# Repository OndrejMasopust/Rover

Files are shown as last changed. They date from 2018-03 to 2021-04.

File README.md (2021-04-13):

# Rover
This repository contains my school project. It is a remote control car with rotating lidar. The car is controled from a custom Java app.   
If you want the documentation to be translated into English, raise an issue and I will try to translate it as soon as possible. ;-)

[Link](https://ondrejmasopust.github.io/Rover/) to the official website with a documentation.

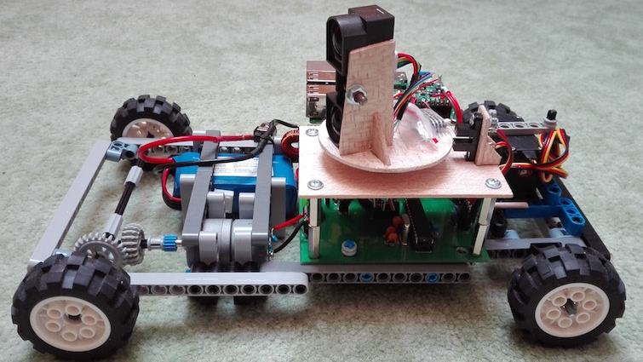
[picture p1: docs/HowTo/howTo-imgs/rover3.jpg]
Rover
   
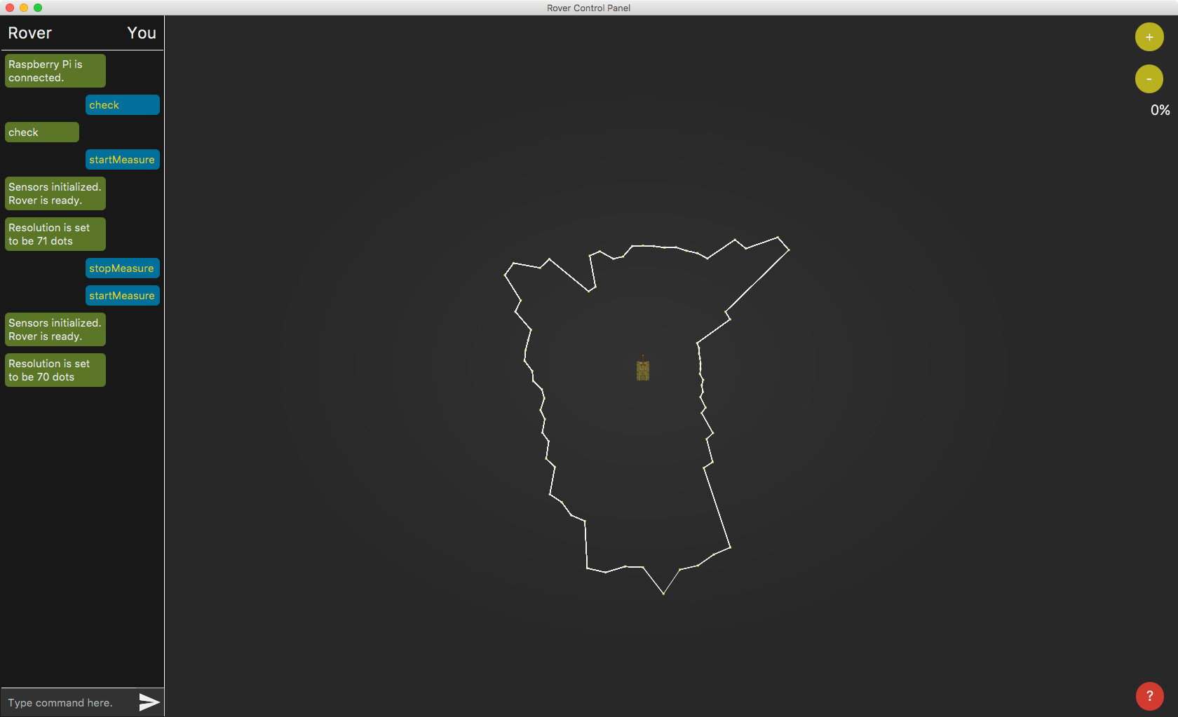
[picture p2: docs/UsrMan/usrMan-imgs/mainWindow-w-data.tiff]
main-Screen-w-data


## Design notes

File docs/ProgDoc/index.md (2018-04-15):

# Programátorská dokumentace
[Java dokumentace](JavaDoc/index.html)   
[Python dokumentace](PythonDoc/index.html)   
[C dokumentace](CDoc/index.html)

`Jar` soubor s řídící aplikací je možné najít na [tomto odkazu](https://github.com/OndrejMasopust/Rover/blob/master/Java/build/dist/RoverControlPanel.jar).   
Program pro Raspberry Pi lze nají v [této složce](https://github.com/OndrejMasopust/Rover/tree/master/Python/src) (složky s názvem `test` nejsou pro běh programu nutné).   
Firmware pro ATMega 168 je na [tomto odkazu](https://github.com/OndrejMasopust/Rover/tree/master/AVR/firmware).

# Popis fungování

## Autíčko
### Úvod
Autíčko je postavené nad platformou Raspberry Pi, která obstarává většinu operací. Jako programovací jazyk pro Raspberry jsem si zvolil Python, jelikož je pro tuto platformu nejvíce podporován.
Pro konverzi analogových dat ze senzoru do digitální podoby je použit mikrokontrolér ATMega 168 od firmy MicroChip.
Obousměrný provoz motorů obstarává integrovaný obvod L293D od firmy Texas Instruments.

### Napájení
Celé autíčko je napájeno baterií typu Li-pol se 3
články a kapacitou 1300mAh. Provozní doba autíčka na jedno nabití by teoreticky mohla být klidně přes 2 hodiny (průměrná spotřeba byla naměřena okolo 500mAh). Konverzi napětí z úrovně baterky na
úroveň "příjemnou" obvodům a motorům obstarávají integrované obvody LM2576 též od firmy Texas Instruments. Jsou použity dvě verze tohoto obvodu. První verze je pro konverzi napěťové úrovně na
fixní napětí 5V pro napájení "logiky". Druhá verze s nastavitelným výstupním napětím dodává 6V pro napájení motorů. Tyto obvody vyžadují několik dalších pasivních součástek pro správné fungování.
Ty jsou na plošném spoji v blízkosti samotných LM2576 (oblasti okolo cívek).

Obvody LM2576 jsou tzv. spínané zdroje napětí. To znamená že výstupní napětí je upravováno pomocí PWM (pulse width modulation). To má za důsledek efektivní konverzi napětí (dokumentace uvádí
účinnost až 77%). Dalším druhem napěťových regulátorů jsou tzv. lineární regulátory, které ovšem fungují v podstatě jako proměnné rezistory a nejsou tudíž moc efektivní. Přebytečnou elektrickou
práci vyzáří ve formě tepla. Proto jsem se rozhodl pro spínaný zdroj oproti lineárnímu regulátoru.

### Zatáčení
Zatáčecí mechanismus je řešen servem od firmy Hitec. Mechanismus zatáčení jsem okopíroval z Lego stavebnice
["Dump Truck"](https://www.lego.com/en-us/service/buildinginstructions/search?initialsearch=8415#?text=8415). Servo je ovládáno z Raspberry Pi pomocí tzv. PWM (pulse width modulation). Jelikož je
pro ovládání serva potřeba velké preciznosti signálu, zvolil jsem pro tento účel knihovnu [pigpio](http://abyz.me.uk/rpi/pigpio/). Tato knihovna poskytuje API, které umožňuje
snadné ovládání serva zadáním délky služebního cyklu (duty cycle). Pro hodnotu `1500` se ručička serva nastaví do střední polohy. Bezpečné meze otáčení z hlediska serva je interval <1000; 2000>.
Ovšem pro konkrétní potřeby Roveru je tento interval omezen.

### Pohyb
Pohyb autíčka obstarává stejnosměrný motor uložený vedle baterie. K jeho ovládání je použit již zmíněny obvod L293D. Ten přijímá signál PWM (pulse width modulation) od Raspberry a podle toho je
schopen upravit napětí proudící do motoru. Možnosti měnit napětí jdoucí do motoru není ovšem využito. Do motoru tedy jde buď 6V, nebo 0V.

L293D ovšem obstarává ještě jednu důležitou funkci a tou je možnost změny polarity výstupu k motoru a tudíž změna směru otáčení motoru. Toho je docíleno pomocí tzv. "H můstku" (H-bridge)
uvnitř L293D. Pro jistotu je k němu připojen pasivní kovový chladič jako prevence přehřátí.

### Senzor
Jako senzor vzdálenosti jsem použil výrobek firmy Sharp. Konkrétně ten s označením `GP2Y0A710K0F`. Měří vzdálenost pomocí paprsku světla. Jeho nevýhodou ovšem je, že má rozsah jen 100cm až 500cm.
Vzdálenosti menší než 100cm se budou na výstupu jevit jako vyšší a nelze je odlišit. Pro měření vzdáleností kratších než 100cm by bylo potřeba využít jiného senzoru.

Rotace senzoru je řešena pomocí stejnosměrného motoru. Přenos dat z rotujícího senzoru je řešen pomocí tzv. "slip ring". Ten umožňuje elektrický kontakt mezi dvěma navzájem rotujícími objekty.
Jelikož je motor stejnosměrný a není tedy žádná zpětná vazba ohledně jeho aktuální polohy, obsahuje držák senzoru i optozávoru. Ta se stará o informování Raspberry o tom, že senzor vykonal jednu
otáčku. Optozávora se skládá z LED diody a fototranzistoru. Když je paprsek světla z diody do tranzistoru přerušen výstupkem na senzorovém kotouči, tranzistor se uzavře a tím vyšle signál do
Raspberry. To je uvnitř nastaveno tak, aby tyto signály zpracovalo náležitým způsobem.

Aby mohla řídící aplikace správně vizualizovat data, je nutné na začátku měření provést několik "volných otáček", kdy nejsou data ze senzoru vyžadována. Během těchto rotací se motor dostane na
konstantní rychlost otáčení a v Raspberry Pi je změřena doba jedné otáčky na základě prodlevy signálů z optozávory. Ta je poté vydělena dobou jednoho měření senzoru a výsledkem je počet měření
během jedné otáčky. Jedno měření trvá dle dokumentace přibližně 20ms a s touto hodnotou se také pracuje v programu. Jiná možnost, jak být od senzoru upozorněn na novou naměřenou hodnotu není.

Vypočítané rozlišení se poté
pošle řídící aplikaci a slouží ke správnému umístění později přijatých dat na obrazovku. Raspberry také po každém vykonání otáčky senzoru pošle do řídící aplikace příkaz k resetování indexu měření,
aby aplikace znovu začala umisťovat naměřená data od počátečního pozice a nedošlo k pootočení obrazu vykreslovaném v aplikaci (více o tom později).

Výstup
senzoru je řešen analogově. Podle naměřené vzdálenosti se mění úroveň napětí na výstupu. O konverzi toho analogového výstupu do digitální podoby se, jak už jsem zmínil, stará mikrokontrolér ATMega
168.

### ATMega 168
Mikrokontrolér ATMega 168 je naprogramován v jazyce C a k jeho časování je použit krystal o frekvenci 16MHz. Komunikace s Raspberry Pi je řešena pomocí protokolu I<sup>2</sup>C. Raspberry Pi je
v této komunikace v roli tzv. "master" a ATMega jako tzv. "slave". Jelikož ATMega není schopno
vykonávat více procesů najednou, je jeho program řešen pomocí tzv. přerušení (interrupts). Na samotném začátku programu je provedena jedna konverze, která se uloží a ATMega čeká na pokyn od Raspberry. Když
si Raspberry vyžádá data, ATMega mu pošle data z poslední konverze a provede konverzi novou. Poté znovu čeká na vyžádání dat přes I<sup>2</sup>C. Komunikaci přes I<sup>2</sup>C je na straně
Raspberry Pi řešena pomocí knihovny [smbus2](https://pypi.python.org/pypi/smbus2/0.2.0).

Zpracování dat v Raspberry Pi spočívá v přepočtení přijaté relativní hodnoty na volty a poté pomocí dané funkce přepočtení voltů na centimetry. Funkce byla stanovena pomocí
zpracování pokusných naměřených hodnot v programu Microsoft Office Excel. Přepočtená data se posílají přes TCP protokol do řídící aplikace na operátorově počítači, kde se vizualizují.

### Příkazy
Příkazy, které může Rover řídící aplikaci posílat jsou následující:

#### rd
Tento příkaz slouží k informování operátora o tom, že již byly provedeny "volné otáčky". Jde o zkratku slova "ready".

#### ro
Příkaz `ro` je vždy následován celou číslovkou, která označuje počet měření během jedné otáčky. Tento příkaz je spolu s příkazem `rd` posílán vždy po dokončení "volných otáček". Příkaz zvolen
jako zkratka slova "resolution".

#### dt
Příkaz `dt` slouží k přenosu naměřených hodnot. Je následován celou číslovkou označující vzdálenost v centimetrech. `dt` je zkratka slova data.

#### rc
Tento příkaz je poslán Roverem vždy po dokončení jedné otáčky a instruuje řídící apliakci, že následující data má zobrazovat od počátečního bodu s indexem 0. Jde o synchronizaci, aby nedošlo k
pootočení vizualizovaného obrázku (více o tom později). Jde o zkratku slovního spojení "reset dot counter".

#### er
Příkaz `er` je vždy následován chybovou hláškou, která se má zobrazit v konzoli řídící aplikace. Tato zpráva bude v červené bublině, aby se odlišilo, že jde o chybu. `er` je zkratka pro "error".

#### bt
Tento příkaz zatím Rover neposílá, ale řídící aplikace ho umí zpracovat. Jde o změnu ukazatele stavu baterie v řídící aplikaci. Zpětná vazba o stavu baterie není v zadání práce a není zatím funkční.
Příkaz by měl být vždy následován číslem, které se má v ukazateli zobrazit a byl zvolen jako zkratka slova "battery".

## Řídící aplikace
Řídící aplikace je naprogramována v jazyce Java. Grafické rozhraní je vytvořeno pomocí API JavaFx. Neúspěšný pokus o navázání komunikace s Roverem je na začátku běhu programu řešen nekonečnou
smyčkou, kdy se program stále snaží komunikaci navázat. Pokud chce uživatel zastavit pokusy o navázání komunikace, musí sám aplikaci ukončit. Jak již bylo zmíněno v uživatelské dokumentaci,
ovládací aplikace obstarává vizualizaci dat ze senzoru a bezdrátové ovládání pohybu autíčka.

Po připojení k Roveru běží aplikace na 2 vláknech. První se stará o grafické rozhraní a to druhé o přijímání zpráv od Roveru. Pokud přijde zpráva od Roveru, komunikační vlákno ji předá grafickému
vláknu, které poté zprávu buď zobrazí v konzoli na levé straně obrazovky, nebo vykoná daný příkaz. Některé příkazy od Roveru se v konzoli nezobrazují z úsporných důvodů.

### Systém vizualizace dat
Data z měření jsou z Roveru posílána bez informace o jejich úhlové poloze. Jedinou synchronizaci poskytuje příkaz `rc`. Z tohoto důvodu si řídící aplikace spočítá úhel mezi jednotlivými měřeními na
základě přijatého rozlišení (příkaz `ro`) poté, co Rover dokončí "volné otáčky". Tento úhel se nadále používá pro všechna přijatá měření. Řídící aplikace si ukládá vlastní čítač dat, který se
vždy zvýší o jedno s každou přijatou hodnotou.
Na základě tohoto čítače je nastaven úhel zobrazených dat. Čítač je resetován po přijetí příkazu `rc` a následující přijaté měření je zobrazeno pod úhlem 0° (pozice za Roverem).

Pokud je předchozí měření viditelné, je spojeno s aktuálním měřením pomocí úsečky. To pomáhá představě o půdorysu okolí Roveru.

Vizualizovaná data je možné si přiblížit a oddálit pomocí tlačítek "+" a "-" v pravém horním rohu aplikace.

### Ovládání pohybu Roveru
Ovládat pohyb Roveru je možné z řídící aplikace pomocí mačkání šipek na klávesnici. Pokud je ovšem zrovna prováděna akce zápisu do textového pole pro zadávání příkazů, mačkání šipek nebude mít efekt
ovládání pohybu Roveru. Proto je vždy po odeslání příkazu z textového pole zaměření z toho textového pole odňata, aby bylo možné šipkami pohyb Roveru ovládat.

### Příkazy
Příkazy, které budou mít nějaký efekt po jejich zadání v řídící aplikaci jsou zobrazeny v konzoli žlutým fontem a jsou následující:

#### startMeasure
Tento příkaz instruuje Rover o tom, že má inicializovat senzorový motor a začít posílat data z měření.

#### stopMeasure
Příkaz `stopMeasure` naopak měření zastaví.

#### check
Teto příkaz slouží k ověření komunikace mezi Roverem a řídící aplikací. Pokud Rover ihned odpoví zprávou `check`, je spojení v pořádku. Pokud ne, nastala někde chyba.

#### $resPer
Příkaz `$resPer` slouží k resetování stavu baterie na 100%. Dolar na začátku značí, že jde pouze o interní příkaz. Tento příkaz není odesílán autíčku.

### Informační stránka
V aplikaci je v pravém dolním rohu tlačítko s otazníkem. To slouží ke zobrazení stručné informace ohledně příkazů popsaných výše.

# Zdroje

### Knihovny nestandardní pro použité programovací jazyky
- [Pigpio](http://abyz.me.uk/rpi/pigpio/)
- [smbus2](https://pypi.python.org/pypi/smbus2/0.2.0)
- [RPi.GPIO](https://pypi.python.org/pypi/RPi.GPIO)

### Programy
- [Eclipse IDE](https://www.eclipse.org)
- [Scene Builder](http://gluonhq.com/products/scene-builder/)
- [TextWrangler](https://www.barebones.com/products/textwrangler/)
- [Pandoc](https://pandoc.org)
- [Overleaf](https://www.overleaf.com)
- [ShareLaTex](https://cs.sharelatex.com)
- [Doxygen](http://www.stack.nl/~dimitri/doxygen/)
- [Apache Ant](https://ant.apache.org)
- [Lego Digital Designer](https://www.lego.com/en-us/ldd)

### Tutoriály
Uvedeny pouze ty "nejvíce klíčové" pro můj projekt.
- [JavaFx GUI](https://www.youtube.com/watch?v=FLkOX4Eez6o&list=PL6gx4Cwl9DGBzfXLWLSYVy8EbTdpGbUIG)
- [Java multithreading](https://www.itnetwork.cz/java/vlakna)
- [Python networking](https://www.youtube.com/watch?v=XiVVYfgDolU)
- [Python multithreading](https://www.tutorialspoint.com/python/python_multithreading.htm)
- [Python Event()](https://stackoverflow.com/questions/31247820/how-to-use-event-objects-in-python-with-a-thread)

### Barvy grafického rozhraní
- [Blackberry pallete](https://developer.blackberry.com/design/bb10/color.html)

### Webová stránka
Použito služby [GitHub Pages](https://pages.github.com)

### Obrázky
#### Odesílací šipka v hlavním okně řídící aplikace
<div>Icons made by <a href="https://www.flaticon.com/authors/google" title="Google">Google</a> from <a href="https://www.flaticon.com/" title="Flaticon">www.flaticon.com</a> is licensed by
<a href="http://creativecommons.org/licenses/by/3.0/" title="Creative Commons BY 3.0" target="_blank">CC 3.0 BY</a></div>
#### Obrázek tanku v hlavní okně řídící aplikace
Autor nevyžaduje být uveden. Uvedu tedy alespoň [odkaz na webovou stránku](http://2dgameartforfree.blogspot.cz/2014/09/top-down-extras-2-tank.html), kde lze obrázek stáhnout.

### Ostatní zdroje
Se schématem plošného spoje mi pomohl Ondřej Dvorský.   
S vyladěním programu pro Raspberry Pi mi pomohl vedoucí práce Vojtěch Horký.   
Oběma patří velké poděkování.

Výrobu plošného spoje obstarala firma [JLCPCB](https://jlcpcb.com).

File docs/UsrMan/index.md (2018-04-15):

# Rover
Rover je dálkově řízené autíčko s otočným lidarem. Ovládací aplikace umožňuje vizualizaci dat ze senzoru a ovládání autíčka.

## Autíčko
Hlavní konstrukce autíčka je sestavená z lego kostiček. Návod na sestavení můžete najít [zde](https://ondrejmasopust.github.io/Rover/HowTo/index.html). K sestavení je nutná znalost pájení.

Autíčko se zapne přepnutím přepínače vedle baterie. V tu chvíli by měly indikační LED diody na Raspberry Pi začít blikat. Je nutné chvíli počkat, než se Raspberry Pi načte a poté je možné
se k autíčku připojit přes Wi-Fi (stejně, jako byste se připojovali k běžné Wi-Fi např. u vás doma). V tuto chvíli ovšem není ještě možné autíčko ovládat. Je nutné spustit danou aplikaci, která
má běžet na Raspberry Pi. Toho se docílí tak, že se připojíte k Raspberry Pi přes `ssh` pomocí příkazové řádky:
```
ssh pi@raspberrypi.local
```
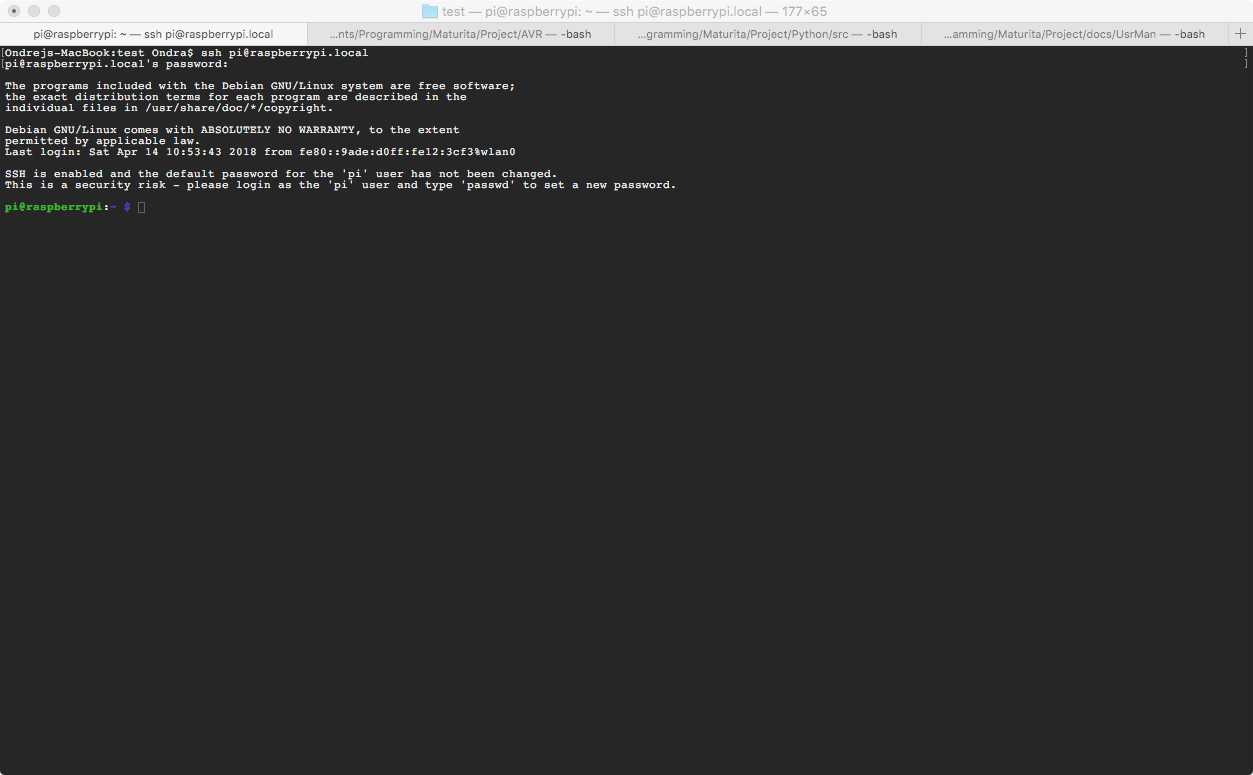
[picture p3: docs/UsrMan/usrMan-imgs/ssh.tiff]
ssh
   
Budete vyzváni k zadání hesla. Znaky se nebudou zobrazovat na obrazovce během toho, jak je budete zadávat. To je běžné chování a je to tak z bezpečnostních důvodů.

Až se přihlásíte do terminálu Raspberry Pi, přejděte pomocí příkazu `cd` do složky se souborem `Main.py`. V mém případě to znamená:
```
cd Documents/Ondra/Rover/src/com/masopust/ondra/python/main/
```
Nyní můžete spustit program pomocí příkazu:
```
python3 Main.py
```
V tuto chvíli program čeká, až se někdo pokusí s ním navázat komunikaci. Toho se docílí v počítačové aplikaci, která je součástí projektu. Pokud se připojení podaří, v terminálu se ukáže
(IP adresa a číslo portu se mohou lišit):
```
Connection from ('192.168.0.6', 54710) was successful
```

## Aplikace
Ovládací aplikace obstarává vizualizaci dat ze senzoru a bezdrátové ovládání pohybu autíčka. Aplikaci
lze spustit dojklikem na soubor `RoverControlPanel.jar`, který lze stáhnout [zde](https://github.com/OndrejMasopust/Rover/blob/master/Java/build/dist/RoverControlPanel.jar). Po spuštění aplikace budete vyzvání k zadání IP adresy autíčka a portu, přes který se chcete zkusit
k Raspberry Pi připojit. Pokud neznáte IP adresu autíčka, lze zadat `raspberrypi.local`. To by mělo též fungovat. Jako port uveďte číslo `5321`, pokud jste toto číslo nezměnili v programu, který
běží na Raspberry Pi. Po zadání hodnot stiskněte tlačítko `Connect`, nebo stiskněte `Enter` na vaší klávesnici. Pokud chcete program zavřít, stiskněte tlačítko `Cancel`, nebo křížek.   
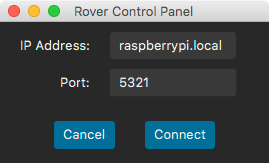
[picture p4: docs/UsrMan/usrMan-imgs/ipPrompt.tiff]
ipPrompt
   
Dále se zobrazí okno, které zobrazuje stav připojování k Roveru. Pokud vše probíhá hladce, neobjeví se žádná hláška v černém obdélníku:   
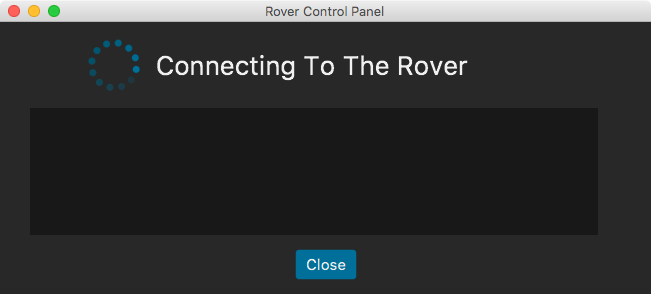
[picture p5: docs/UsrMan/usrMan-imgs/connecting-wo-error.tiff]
connecting-wo-error
   
Pokud je něco v nepořádku, vypíše se popis chyby v černém obdélníku:
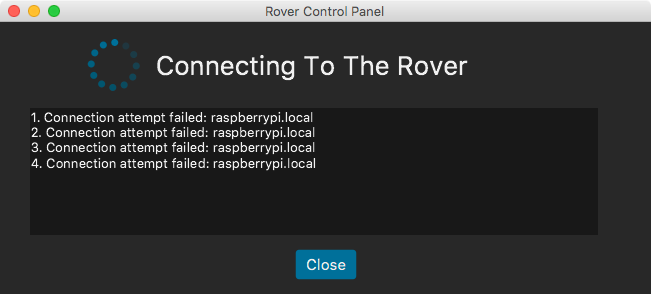
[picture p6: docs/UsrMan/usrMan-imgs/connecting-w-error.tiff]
connecting-w-error
   
Pokud se vám podaří připojit úspěšně k autíčku, dostanete se do hlavního okna a v konzoli se vám objeví zpráva od Roveru, že spojení proběhlo úspěšně:
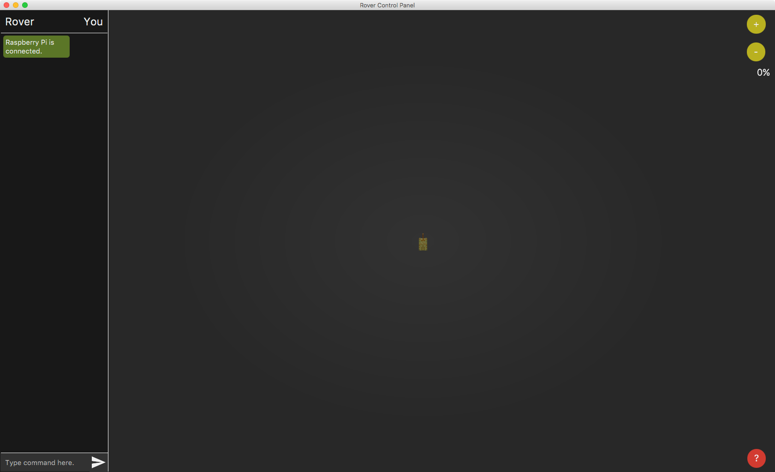
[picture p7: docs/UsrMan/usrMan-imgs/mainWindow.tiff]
mainWindow
   
Uprostřed okna se zobrazí malý obrázek tanku, který symbolizuje váš Rover.

Nyní můžete ovládat Rover dle libosti. Mačkáním šipek můžete uvádět Rover do pohybu (vzad i vpřed) a zatáčet. Příkazy lze zadávat přes konzoli v levé části okna. Do textového pole v levém dolním
rohu napište zprávu, kterou chcete odeslat a poté stiskněte `Enter`, nebo myší stiskněte šipku vpravo od textového pole. Vámi zadaná zpráva se objeví v konzoli zarovnaná doprava, což značí, že
jste zprávu odeslali vy. Pokud se objeví zpráva zarovnaná doleva, je to zpráva od autíčka. Příkazy poslané od vás autíčku, které vyvolají nějakou akci se v bublině zobrazí žlutým fontem. Lze tak
ověřit správné napsání příkazu.

Pokud Roveru odešlete přes konzoli příkaz `startMeasure`, spustí se
snímání okolí senzorem. Snímání lze zastavit odesláním příkazu `stopMeasure` stejným způsobem. Také lze poslat Roveru příkaz `check`. Tím lze ověřit připojení. Pokud Rover ihned odpoví
zprávou se zněním `check`, spojení je v pořádku. Pokud ne, je někde problém a spojení s autíčkem bylo z nějakého důvodu přerušeno. Další funkce jsou popsány na obrázku:   
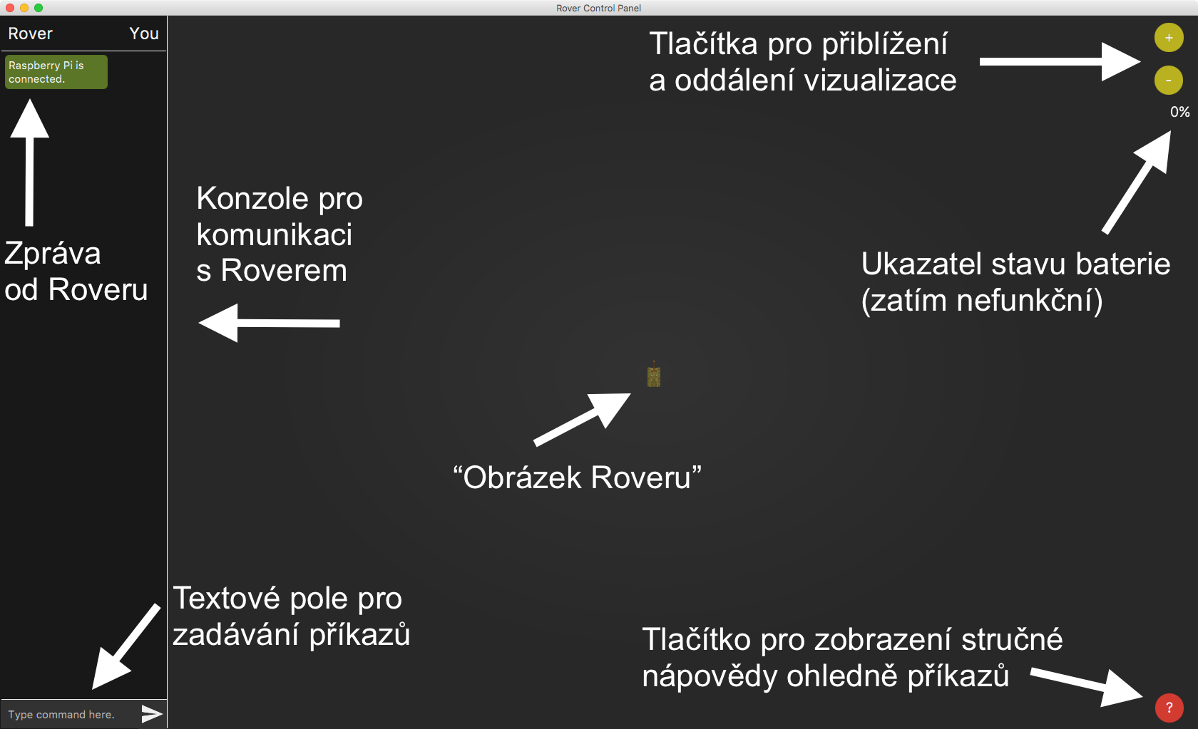
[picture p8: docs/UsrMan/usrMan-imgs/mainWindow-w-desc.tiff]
mainWindow-w-desc
   
Ukazatel stavu baterie zatím není funkční (není v zadání práce), je zde pouze připravený pro budoucí možné rozšíření.   
Stručná informační stránka vypadá takto:   
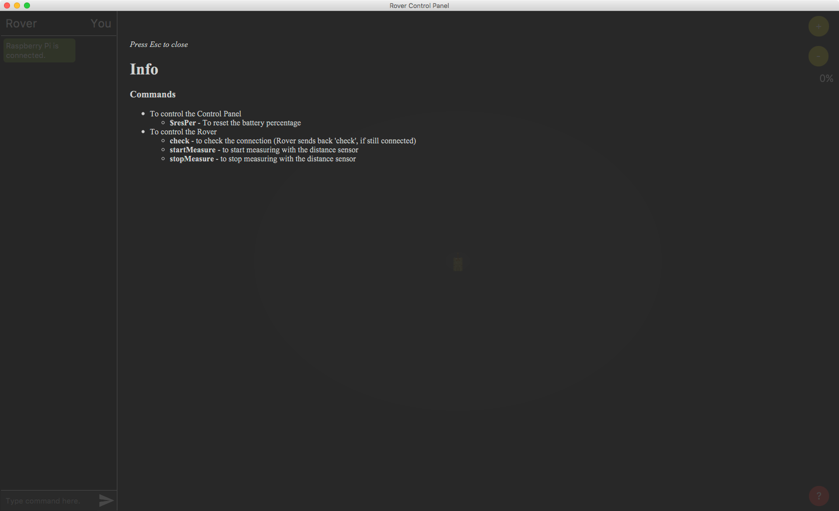
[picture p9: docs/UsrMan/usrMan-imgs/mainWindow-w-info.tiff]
mainWindow-w-info
   
Vizualizace dat ze senzoru může vypadat například takto:
mainWindow-w-data   
Na vizualizaci můžeme jasně rozpoznat roh vpravo, u kterého se Rover nachází.

Aplikaci můžete zavřít křížkem. Program v Roveru se poté sám ukončí, jelikož dojde k přerušení komunikace.

## Technická upozornění
- Nesahejte na jakýkoliv plošný spoj na autíčku po jeho sestavení. Může dojít k poškození statickou elektřinou, zkratu a dalšímu poškození!
- Baterie typu Li-pol jsou výborný sluha v dobrých rukou. Jsou schopné dávat velké proudy a jsou hojně využívány v modelářství. Pokud ovšem nejste seznámeni s jejich riziky,
může dojít ke katastrofě. Pokud jste je nikdy nepoužívali, vysoce doporučuji si o nich přečíst něco na internetu, abyste věděli, do čeho jdete.
- Pokud se ručička serva z nějakého důvodu najednou rychle vychýlí na jednu stranu bez vnějšího signálu (zmáčknutí šipky na klávesnici), je nutné servo hned odpojit z plošného spoje. Pravděpodobně
byla datová linka uzemněna a hrozí poškození serva.
- Pokud se hlavní motor netočí po stisknutí šipky na klávesnici a připojení nebylo přerušeno, je pravděpodobně Rover v pozici, kdy je pro motor nemožné se roztočit pro kladený odpor. Nezkoušejte
v takovém případě dále mačkat šipky na klávesnici. Hrozí poškození motoru.

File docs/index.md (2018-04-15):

[Jak postavit Rover](HowTo/index.html)   
[Uživatelský manuál](UsrMan/index.html)  
[Programátorská dokumentace](ProgDoc/index.html)   
Rover
main-Screen-w-data

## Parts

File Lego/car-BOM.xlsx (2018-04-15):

 | This file was generated with the Lego Digital Designer
Brick | Name | Picture | Part | Color code | Quantity
658201 | RIM Ø36.8X20 |  | 6582 | 1 - White | 4
658126 | TYRE Ø49.6 X 20 |  | 6581 | 26 - Black | 4
4185665 | TECHNIC 2M BEAM |  | 43857 | 23 - Bright Blue | 4
4247727 | TECHNIC 3M BEAM |  | 32523 | 140 - Earth Blue | 2
4227073 | TECHNIC 5M BEAM |  | 32316 | 140 - Earth Blue | 4
4128591 | TECHNIC 5M BEAM |  | 32316 | 23 - Bright Blue | 4
3252426 | TECHNIC 7M BEAM |  | 32524 | 26 - Black | 1
4154767 | TECHNIC 9M BEAM |  | 40490 | 26 - Black | 1
4164358 | TECHNIC 11M BEAM |  | 32525 | 140 - Earth Blue | 4
4164422 | TECHNIC 13M BEAM |  | 41239 | 26 - Black | 3
4193421 | TECHNIC 13M BEAM |  | 41239 | 23 - Bright Blue | 2
6058997 | TECHNIC 15M BEAM |  | 32278 | 140 - Earth Blue | 4
6059010 | TECHNIC ANG. BEAM 3X5 90 DEG. |  | 32526 | 140 - Earth Blue | 2
4106380 | TECHNIC 5M HALF BEAM |  | 32017 | 26 - Black | 1
4260467 | 1/2 BUSH |  | 32123 | 23 - Bright Blue | 10
4109810 | 2M CROSS AXLE W. GROOVE |  | 32062 | 26 - Black | 1
4129886 | CONNECTOR PEG |  | 3673 | 23 - Bright Blue | 60
451926 | CROSS AXLE 3M |  | 4519 | 26 - Black | 1
4225927 | CONNECTOR PEG/CROSS AXLE |  | 6562 | 23 - Bright Blue | 2
4141814 | BUSH FOR CROSS AXLE |  | 6590 | 23 - Bright Blue | 1
4189110 | CONN.BUSH W.FRIC./CROSSALE |  | 43093 | 23 - Bright Blue | 3
4514553 | CONNECTOR PEG W. FRICTION 3M |  | 6558 | 23 - Bright Blue | 2
4512360 | CROSS AXLE, EXTENSION, 2M |  | 59443 | 194 - Medium Stone Grey | 2
4164357 | CATCH W. CROSS HOLE |  | 32039 | 140 - Earth Blue | 1
4227273 | CROSS BLOCK 90° |  | 6536 | 140 - Earth Blue | 1
370626 | CROSS AXLE 6M |  | 3706 | 26 - Black | 2
4185111 | CROSS AXLE 7M |  | 44294 | 26 - Black | 1
370726 | CROSS AXLE 8M |  | 3707 | 26 - Black | 2
4124045 | CROSS AXLE 5,5 WITH STOP 1M. |  | 59426 | 26 - Black | 2
4114670 | TECHNIC STEERING-GEAR 3M |  | 32068 | 26 - Black | 2
4195018 | HTO V BEAM 90 DEGR. |  | 44809 | 140 - Earth Blue | 6
4158925 | TECHNIC CROSSBLOCK 2X3 |  | 32557 | 23 - Bright Blue | 4
4114671 | T. STEERING GEAR, BEARING 2M |  | 32069 | 26 - Black | 2
3226901 | DOUBLE CONICAL WHEEL Z20 1M |  | 32269 | 1 - White | 1
4211434 | CROWN- AND GEAR WHEEL Z24 |  | 3650 | 194 - Medium Stone Grey | 1
Total: |  |  |  |  | 147

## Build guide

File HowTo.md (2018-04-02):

# How to make your own Rover

#### 1. Upgrade your Pi and install the latest version of Python

#### 2. Set up an AP on the Pi
Follow this [tutorial](https://www.raspberrypi.org/documentation/configuration/wireless/access-point.md) to set up your Raspberry Pi as an AP

#### 3. Install these packages on the Pi
In the terminal of the Pi, type:   
```
sudo apt-get install build-essential python-dev
```

#### 4. Enable I<sup>2</sup>C on the Pi
In the Pi terminal, type:
```
sudo raspi-config
```
And there, in "Interafcing Options", select I<sup>2</sup>C and confirm that.
You need to reboot your Pi after this.

#### 5. Install Python smbus2 package
In the Pi terminal, type:
```
sudo pip3 install smbus2
```

#### 6. Install pigpio library
In the Pi terminal, type:
```
wget abyz.co.uk/rpi/pigpio/pigpio.zip
unzip pigpio.zip
cd PIGPIO
make
sudo make install
```

#### 7. Copy the Rover program
Copy the content of the `Rover/Python/` directory somewhere to your Pi.

#### 8. Get the PCB, electronic and Lego parts
...and assemble that.
Buy 4 1nF capacitors more than it is in the schematics. They will be soldered from the motor terminals to the motor shield.   
PCB layout can be found in the `PCBs_schematics/PCB-Layout/` directory. You can order it for example from [JLCPCB](https://jlcpcb.com).   
Some things I used specifically:
-[sensor](https://www.ebay.com/itm/Sharp-GP2Y0A710K0F-IR-Range-Sensor-100-550cm-Infrared-Proximity-Measure-distance/321873113256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)
-[servo](http://hitecrcd.com/products/servos/sport-servos/analog-sport-servos/hs-422-deluxe-standard-servo/product)
-[main motor](https://www.ebay.com/itm/320911868255)
-[sensor motor](https://www.ebay.com/itm/6-12V-100-200-300-30RPM-Mini-DC-Metal-Gear-Motor-Gearwheel-Shaft-Diameter-N20/182498725375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)
(6V 200rpm version)
-[gears](https://www.ebay.com/itm/85Pcs-Plastic-Gears-Rack-Pulley-Belt-Worm-Teeth-Shaft-Car-Toy-Models-Part-DIY/152738933090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)
-Li-Pol 3S 1300mAh battery
-[slip ring](https://www.ebay.com/itm/12-5mm-300Rpm-Capsule-Tiny-Slip-Ring-12-Circuits-Wires-2A-240V-Test-Equipment-/141778019951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)

#### 9. Assemble the sensor holder
I used a balsa wood.   
For example like this:
1. Make bigger hole in the gear, so that it fits the slip ring
3. Make this:   
The diameter of the disc is roughly 6cm.   
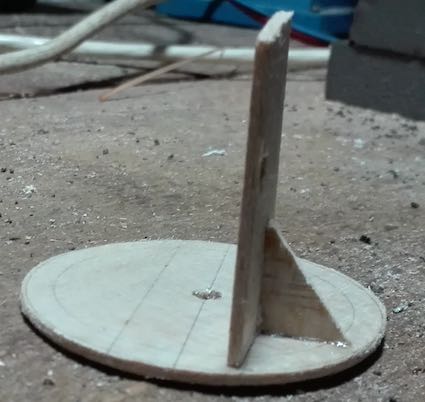
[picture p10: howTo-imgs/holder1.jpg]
holder1

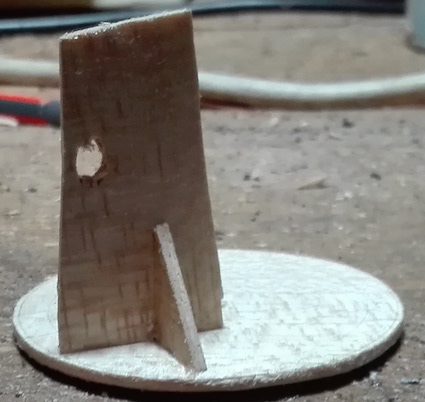
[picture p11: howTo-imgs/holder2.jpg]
holder2

4. Glue a balsa disc to the gear and drill a hole in the middle:   
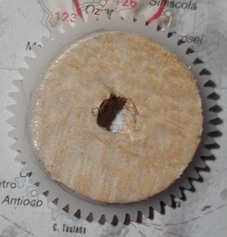
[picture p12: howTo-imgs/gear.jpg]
gear with balsa disc

5. Glue that it to the holder:   
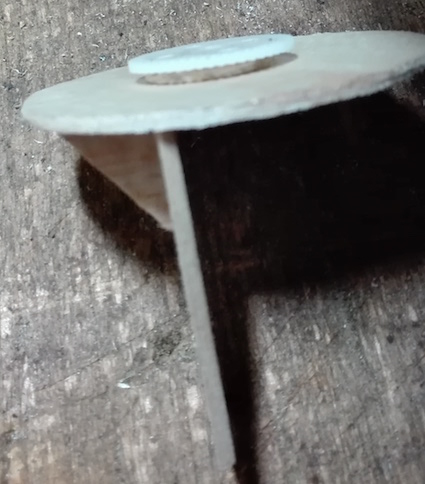
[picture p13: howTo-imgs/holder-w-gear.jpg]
holder with gear

6. Glue the holder to the slip ring.
6. Make a balsa plate:  
The dimensions are roughly 6.5cm x 9.5cm. The holes form a rectangle 8cm x 4.8cm.  
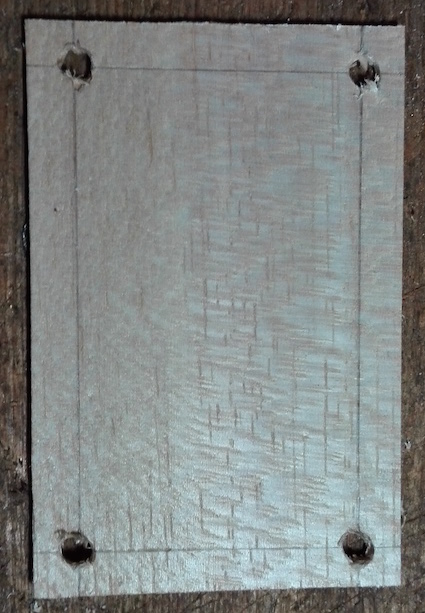
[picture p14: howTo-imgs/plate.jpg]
balsa plate

7. Make a hole in the plate for the slip ring, the motor that rotates with the sensor and the optolatch.
8. Mount the slip ring and the motor (already with its gear) to the plate (I mounted it to a Lego supportive skeleton):   
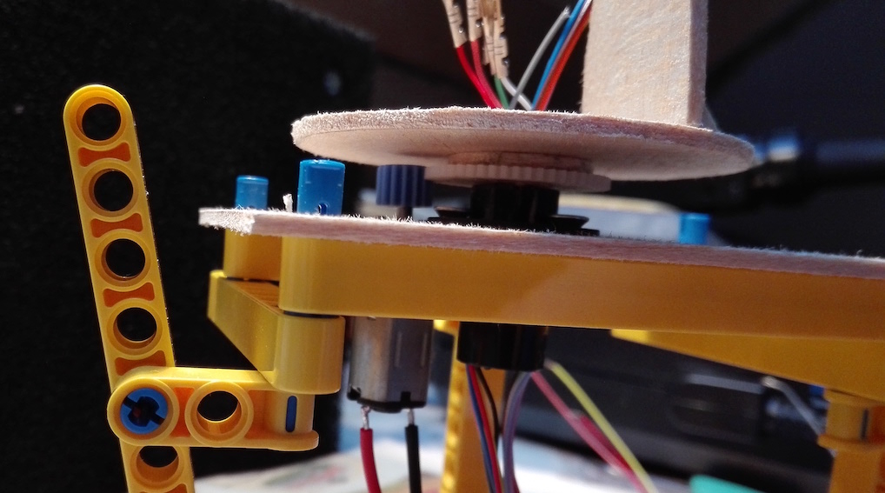
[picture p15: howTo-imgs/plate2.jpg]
plate2
   
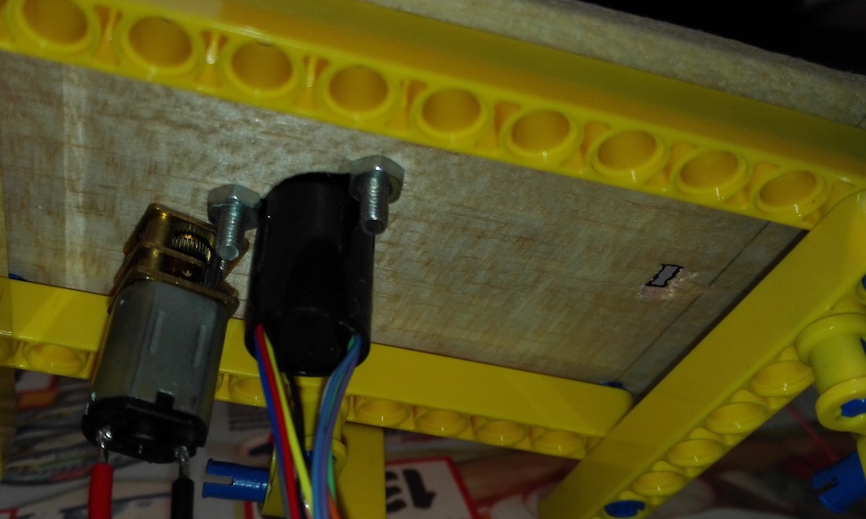
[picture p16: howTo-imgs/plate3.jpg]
plate3

9. Solder a connector for the sensor:  
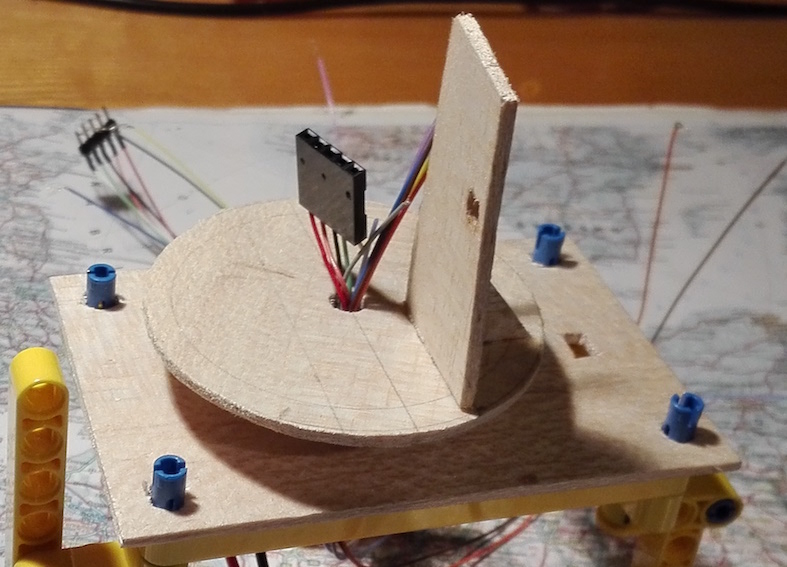
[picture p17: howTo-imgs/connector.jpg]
connector

10. Solder a connector to the wire going from the sensor and screw the sensor to the holder:  
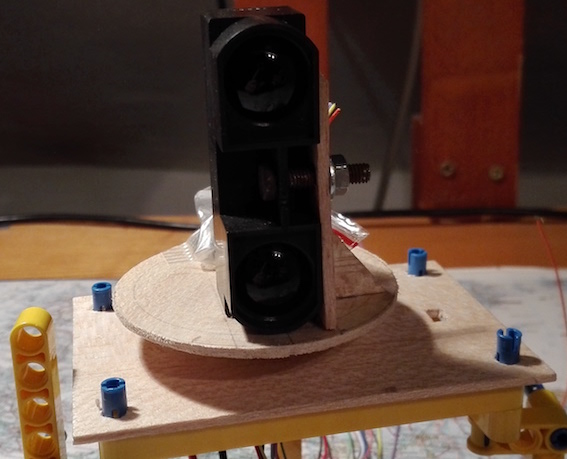
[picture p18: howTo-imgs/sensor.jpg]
sensor

11. Add counterweight to the other side of the holder (I used lead marbles. It should weight the same as the sensor):  
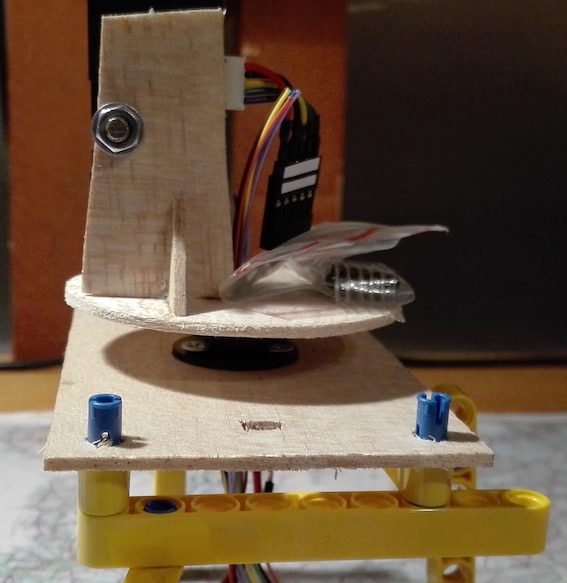
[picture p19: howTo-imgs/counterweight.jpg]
counterweight

12. Create a holder for the opto-latch and mount it:  
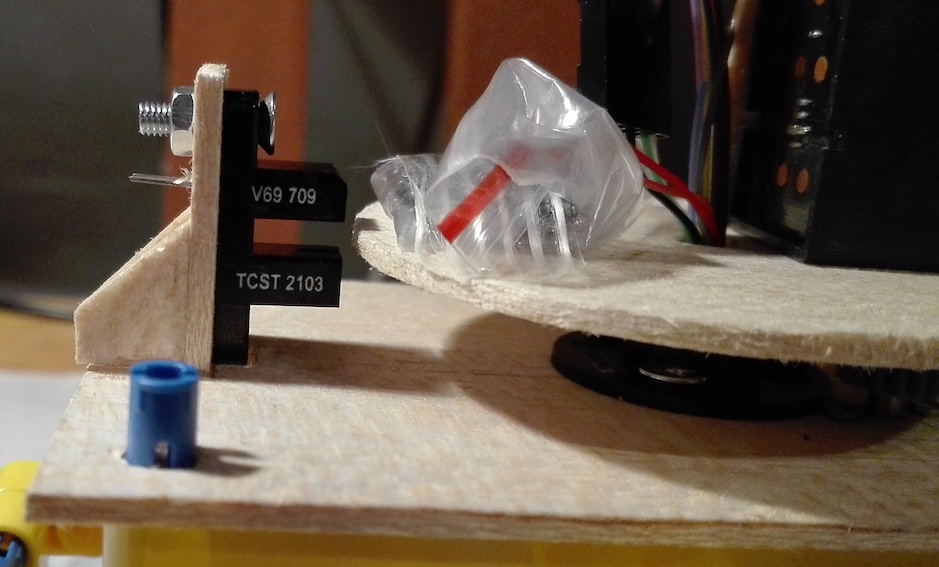
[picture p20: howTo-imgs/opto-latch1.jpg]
opto-latch1
  
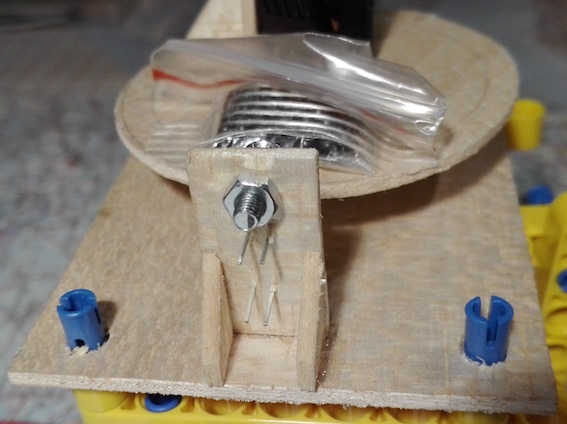
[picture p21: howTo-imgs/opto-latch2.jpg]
opto-latch2
  
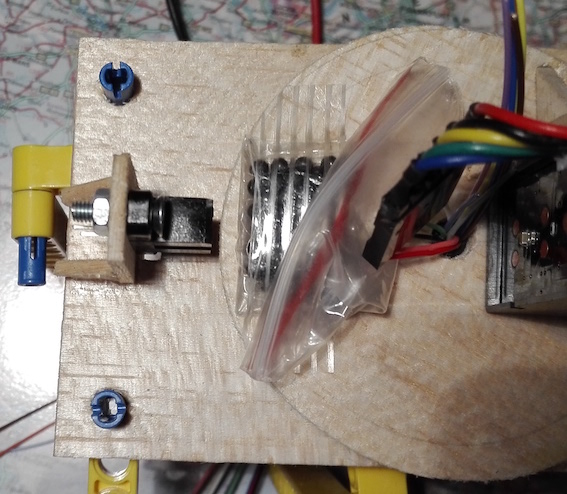
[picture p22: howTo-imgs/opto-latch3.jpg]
opto-latch3

13. Create a protrusion from balsa wood and glue it to the disc. I needs to be in such a way, that it goes through the optolatch in every rotation:  
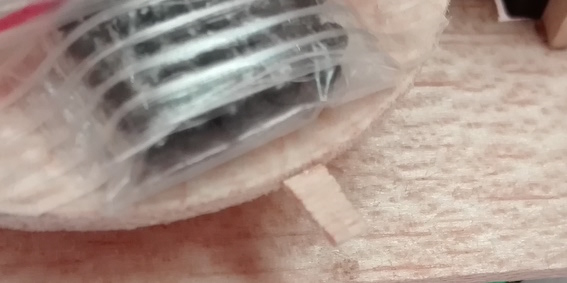
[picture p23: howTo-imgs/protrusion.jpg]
protrusion

14. To strenghten the servo mount, you can glue there a stick with an epoxid glue:  
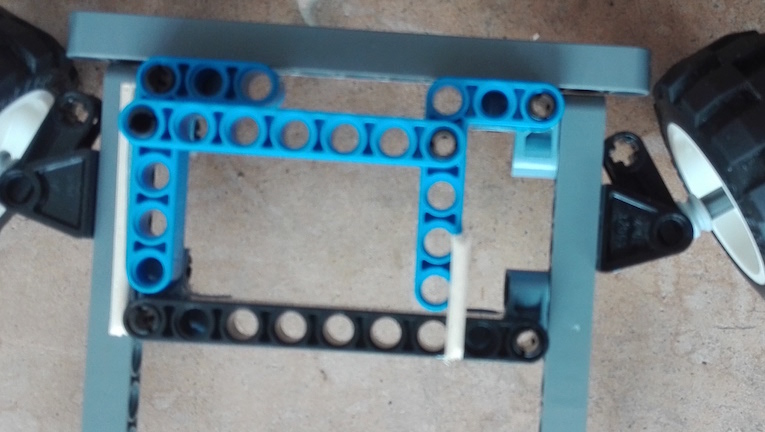
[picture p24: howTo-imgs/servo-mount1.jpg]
stick1
  
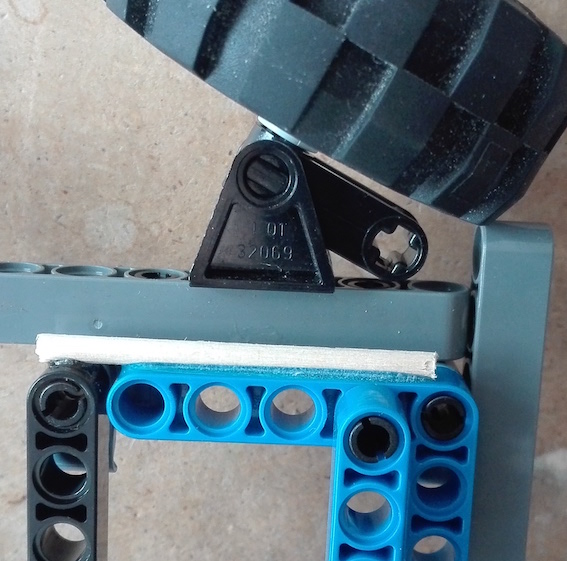
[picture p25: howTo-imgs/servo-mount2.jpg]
stick2

15. Solder the 1nF capacitors between motor terminals and motor shields:
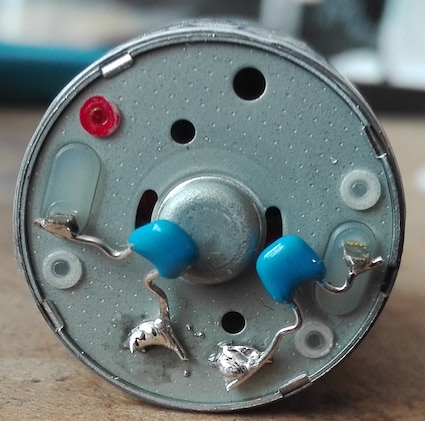
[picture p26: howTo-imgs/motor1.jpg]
motor1
   
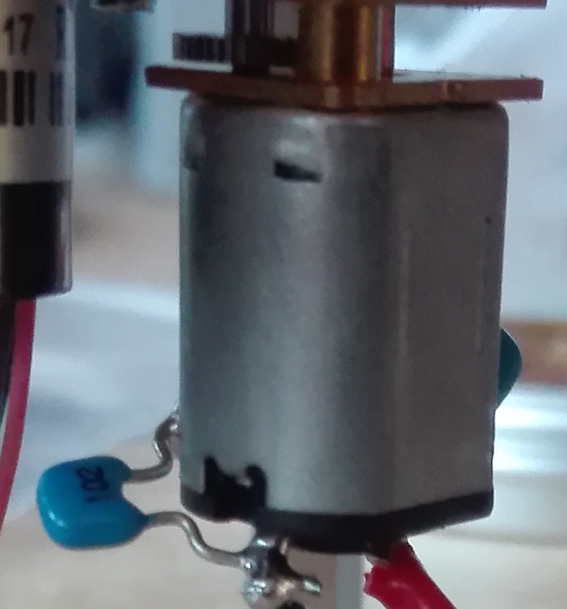
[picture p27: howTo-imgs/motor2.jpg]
motor2

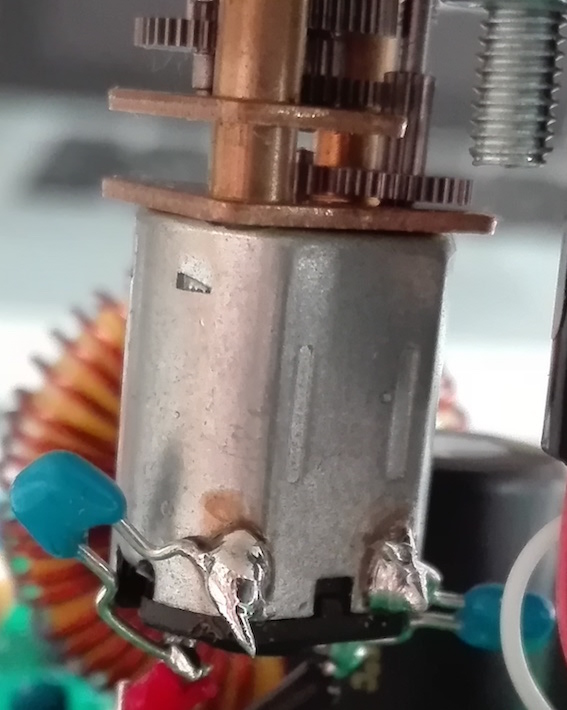
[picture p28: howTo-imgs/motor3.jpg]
motor3


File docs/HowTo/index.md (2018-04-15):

# Stručný návod, jak postavit Rover

#### 1. Zaktualizujte si svoje Raspberry Pi

#### 2. Nastavte si AP na svém Pi
Podle tohoto [tutoriálu](https://www.raspberrypi.org/documentation/configuration/wireless/access-point.md).

#### 3. Nainstalujte si tento balíček na svém Pi
V terminálu spusťte tento příkaz:   
```
sudo apt-get install python-dev
```

#### 4. Povolte I<sup>2</sup>C na Pi
V terminálu spusťte tento příkaz:
```
sudo raspi-config
```
V "Interafcing Options" vyberte I<sup>2</sup>C a potvrďte to.  
Po tomto kroku je potřeba Pi restartovat. (budete vyzváni)

#### 5. Nainstalujte balíček Python smbus2
V terminálu spusťte tento příkaz:
```
sudo pip3 install smbus2
```

#### 6. Nainstalujte knihovnu pigpio
V terminálu spusťte tyto příkazy:
```
wget abyz.co.uk/rpi/pigpio/pigpio.zip
unzip pigpio.zip
cd PIGPIO
make
sudo make install
```

#### 7. Nakopírujte program pro Rover
Nakopírujte obsah složky [Rover/Python/](https://github.com/OndrejMasopust/Rover/tree/master/Python/src) někam do svého Pi. Obsahy složek s
názvem `test` nejsou nutné k běhu programu, proto je můžete vymazat.

#### 8. Pořiďte si plošný spoj, elektronické součástky a Lego kostičky
Potřebujete všechny součástky, které jsou ve schématu.  
Kupte o 4 1nF kondenzátory více, než je v schématu. Budou připájeny mezi vývody motorů a obal motorů.   
Návrh plošného spoje lze najít ve složce [PCBs_schematics](https://github.com/OndrejMasopust/Rover/tree/master/PCBs_schematics). Soubory jsou vytvořeny pomocí
programu [KiCad](http://kicad-pcb.org).   
Plošný spoj si můžete objednat například od [JLCPCB](https://jlcpcb.com). 
V plošném spoji vyvrtejte díry pro držák senzoru a distanční sloupky na Pi. (v těch místech, kde není měď)  
Spájejte plošný spoj a sestavte Lego kostičky podle tohoto [návodu](lego/index.html)   
Až si budete kupovat Lego kostičky, nekupujte "connector pegy" bez třecích výstupků. Konstrukce by pak nebyla tak pevná.  
Některé konkrétní věci, co jsem použil:
- [senzor](https://www.ebay.com/itm/Sharp-GP2Y0A710K0F-IR-Range-Sensor-100-550cm-Infrared-Proximity-Measure-distance/321873113256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)
- [servo](http://hitecrcd.com/products/servos/sport-servos/analog-sport-servos/hs-422-deluxe-standard-servo/product)
- [hlavní motor](https://www.ebay.com/itm/320911868255) (zvolil bych silnější)
- [senzorový motor](https://www.ebay.com/itm/6-12V-100-200-300-30RPM-Mini-DC-Metal-Gear-Motor-Gearwheel-Shaft-Diameter-N20/182498725375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)
(verze 6V 200rpm)
- [převody](https://www.ebay.com/itm/85Pcs-Plastic-Gears-Rack-Pulley-Belt-Worm-Teeth-Shaft-Car-Toy-Models-Part-DIY/152738933090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)
- Li-Pol 3S 1300mAh baterie
- [slip ring](https://www.ebay.com/itm/12-5mm-300Rpm-Capsule-Tiny-Slip-Ring-12-Circuits-Wires-2A-240V-Test-Equipment-/141778019951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)
- [optozávora](https://www.gme.cz/tcst2103)

#### 9. Sestavte držák na senzor
Použil jsem balsové dřevo.
3. Z balsy vyřízněte kotouč o průměru cca. 6cm. Dále malý trojúhelníček jako podpěru a kus balsy, do kterého vyvrtáte díru pro šroub,
kterým přišroubujete samotný senzor - tento kus musí být dost velký na to, aby mohla být díra na správném místě.
Přesné rozměry záleží na velikosti senzoru.    
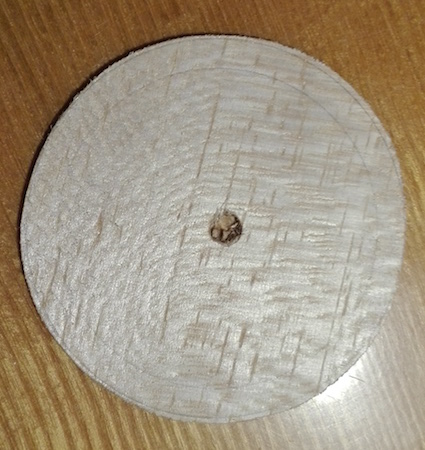
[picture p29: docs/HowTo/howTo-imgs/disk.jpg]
disk

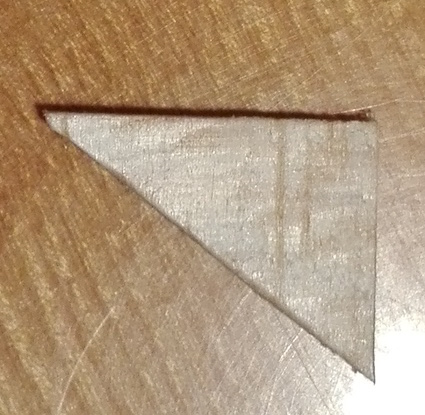
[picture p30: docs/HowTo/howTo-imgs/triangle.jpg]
triangle

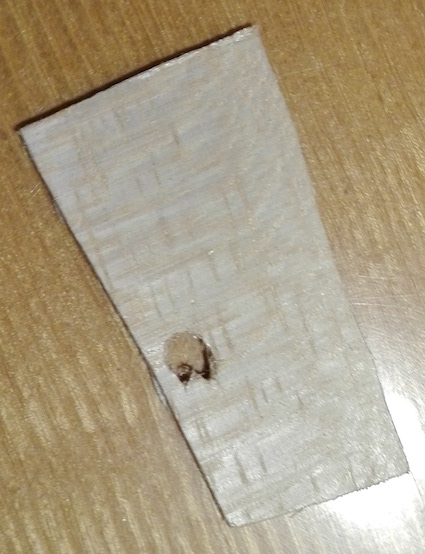
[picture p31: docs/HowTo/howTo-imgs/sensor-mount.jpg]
mount

holder1
holder2
1. V převodu (najdete ho v balíčku převodů v odkazu výše) udělejte větší díru   
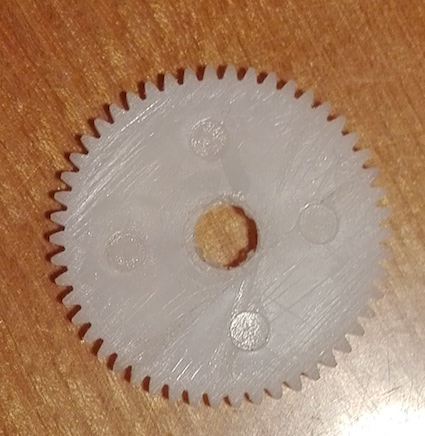
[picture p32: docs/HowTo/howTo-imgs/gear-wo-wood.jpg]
gear

4. Vyřízněte balsový kotouč (o něco menší průměr než převod) a přilepte ho k převodu. Vyvrtejte uprostřed díru:   
gear with balsa disc
5. ...přilepte k držáku:   
holder with gear
6. Přilepte držák ke slip ring (na pozdějších obrázcích je vidět, jak by to mělo vypadat)
6. Udělejte balsovou destičku:  
Rozměry jsou přibližně 6,5cm x 9,5cm. Díry tvoří obdélník o rozměrech cca. 8cm x 4.8cm. Průměr děr je 5mm.  
balsa plate
7. Do destičky udělejte díru pro slip ring, senzorový motor a optozávoru. (jak by to mělo vypadat je opět vidět na následujících obrázcích)
8. Upevněte k destičce slip ring a motor (už s převodem). (Na obrázku jsem si to připevnil na pomocnou konstrukci z Lega):   
plate2   
plate3
9. Připájejte konektor pro senzor:  
connector
10. Připájejete konektor ke kabelu jdoucímu ze senzoru a přišroubujte senzor k držáku:  
sensor
11. Přidejte protizávaží naproti senzoru (Já jsem použil olověné kuličky. Měly by vážit stejně jako senzor):  
counterweight
12. Vytvořte držák pro optozávoru a připevněte ji:  
opto-latch1  
opto-latch2  
opto-latch3
13. Vyřízněte malý jazíček z balsy a přilepte ho ke kotouči. Musí to být uděláno tak, aby při každé otáčce prošel jazíček optozávorou:  
protrusion
15. Připájejte 1nF kondenzátory mezi vývody motorů a obal motorů (jak hlavní motor, tak i motor, co točí senzorem):
motor1   
motor2
motor3   
Teď byste měli mít držák senzoru sestavený.

#### 10. Pro zpevnění držáku na servo k němu můžete přilepit několik špejlí epoxidovým lepidlem:  
stick1  
stick2

#### 11. Připájejte kabely a konektory pro komunikaci Raspberry s ostatními částmi Roveru
(Je dobrý nápad je také označit)   
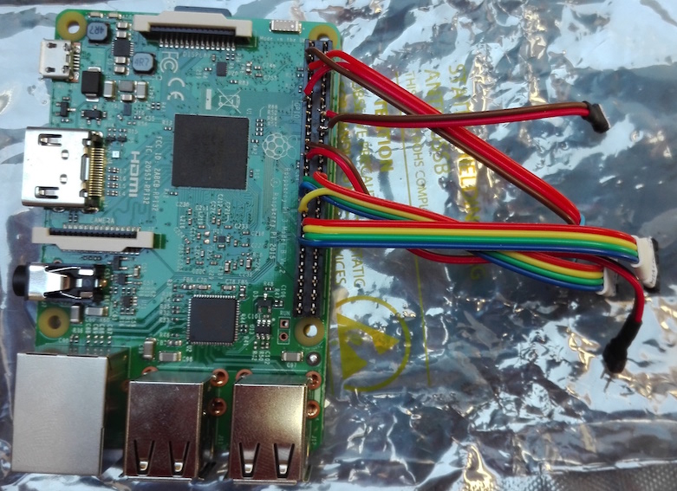
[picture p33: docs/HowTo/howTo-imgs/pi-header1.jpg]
pi header1

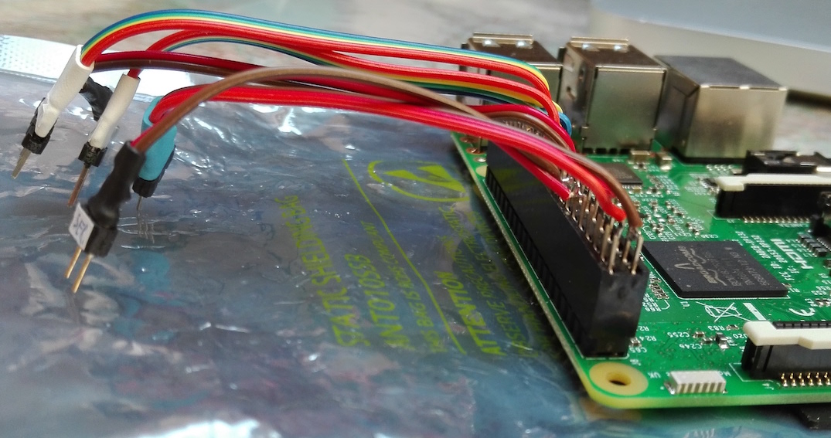
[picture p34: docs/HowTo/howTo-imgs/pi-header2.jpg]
pi header2


#### 12. Připevněte Pi a senzor k plošnému spoji
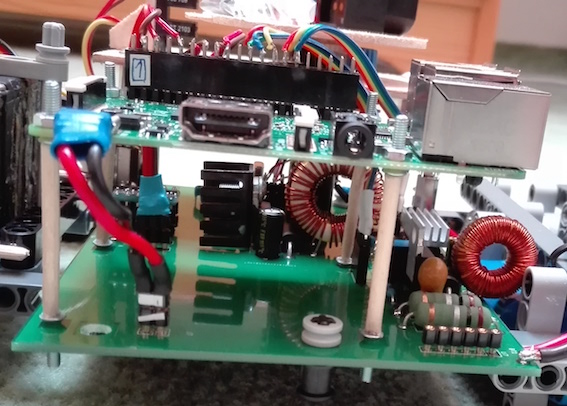
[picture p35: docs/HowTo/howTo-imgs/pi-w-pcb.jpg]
pi-w-pcb

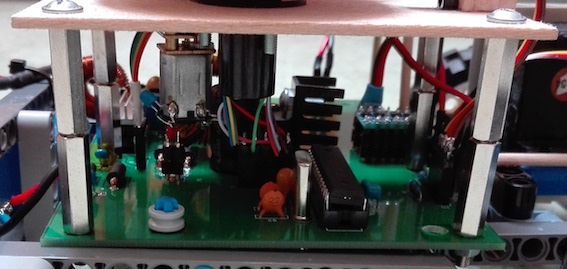
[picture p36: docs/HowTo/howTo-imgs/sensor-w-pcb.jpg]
sensor-w-pcb


#### 13. Všechno sestavte
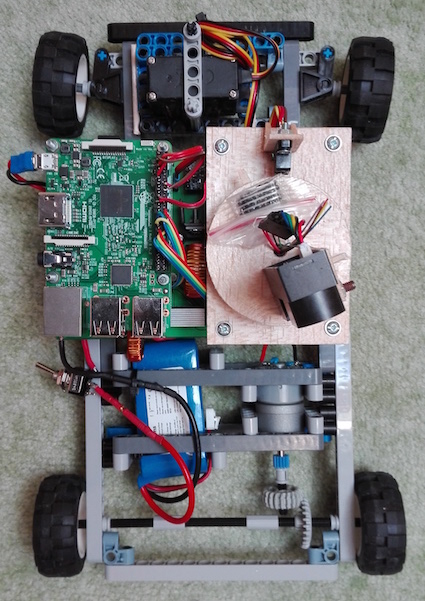
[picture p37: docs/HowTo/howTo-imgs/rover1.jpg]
rover1

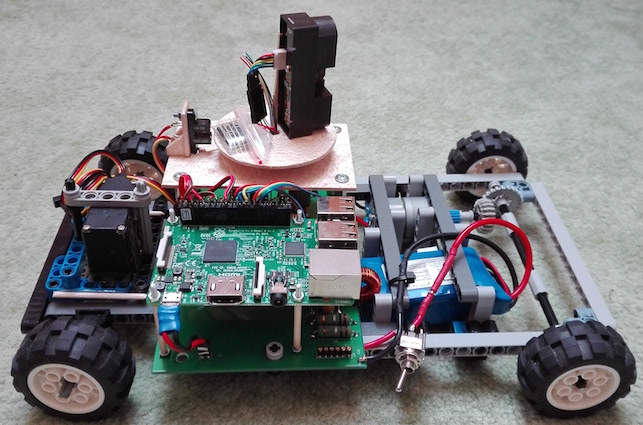
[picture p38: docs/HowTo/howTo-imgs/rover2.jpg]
rover2

rover3
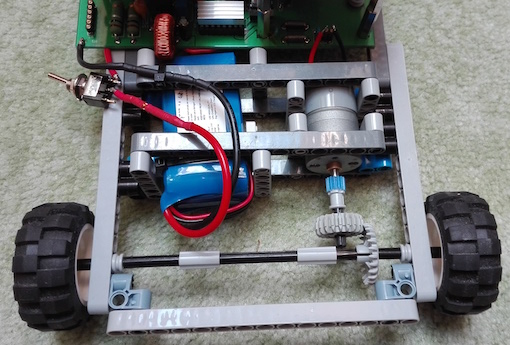
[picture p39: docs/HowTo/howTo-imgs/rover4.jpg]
rover4

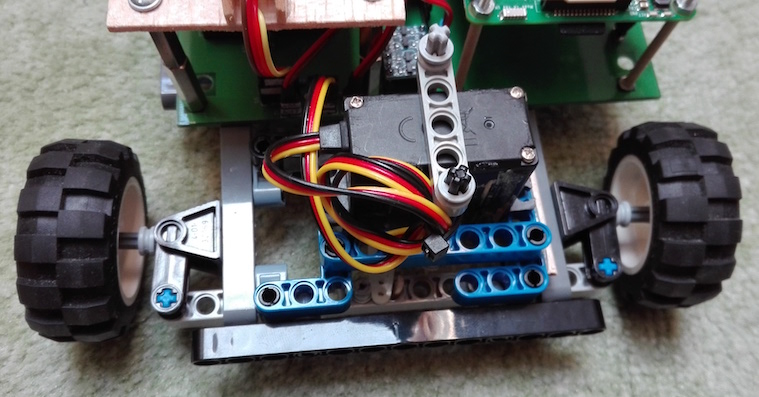
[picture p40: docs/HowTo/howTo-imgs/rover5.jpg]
rover5

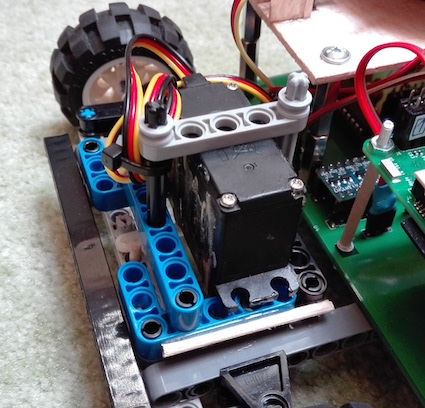
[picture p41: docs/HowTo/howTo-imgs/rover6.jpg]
rover6

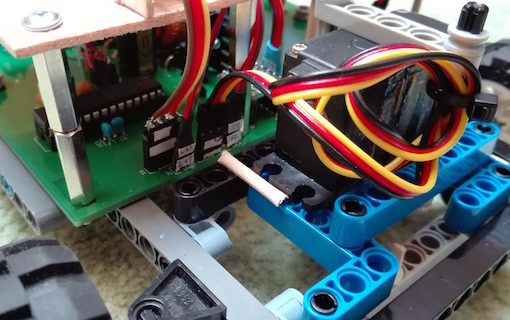
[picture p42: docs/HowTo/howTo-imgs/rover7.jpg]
rover7
   
...a je to!

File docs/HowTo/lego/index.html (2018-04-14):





Model Name:
car-design

Number of Bricks: 147

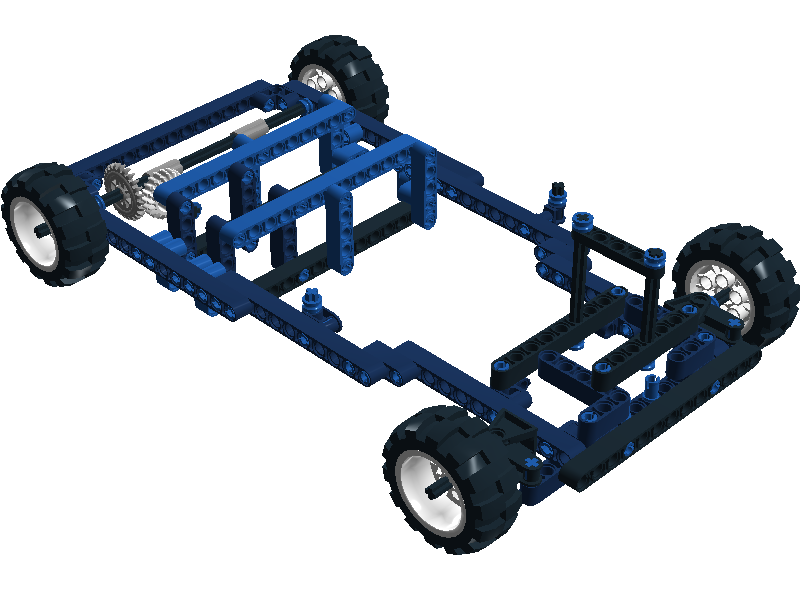
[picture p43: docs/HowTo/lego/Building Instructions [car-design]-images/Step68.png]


Step 1 of 68

- 1 x
- 
- 1 x
- 
- 1 x
- 

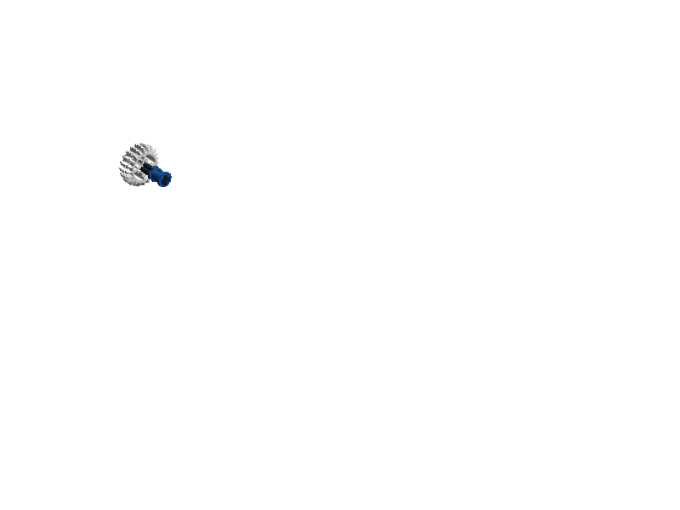
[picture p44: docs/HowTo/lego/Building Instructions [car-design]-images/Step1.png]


Step 2 of 68

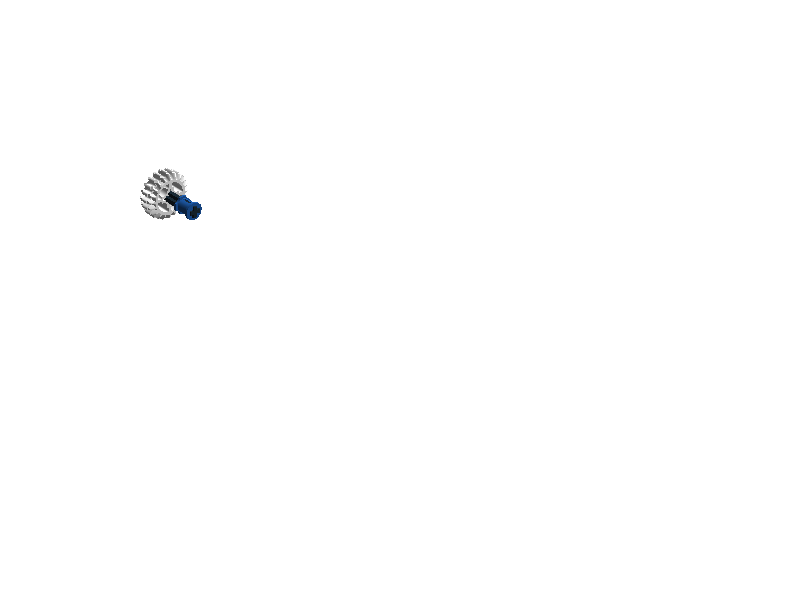
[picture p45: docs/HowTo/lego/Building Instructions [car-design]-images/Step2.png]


Step 3 of 68

- 1 x
- 
- 2 x
- 

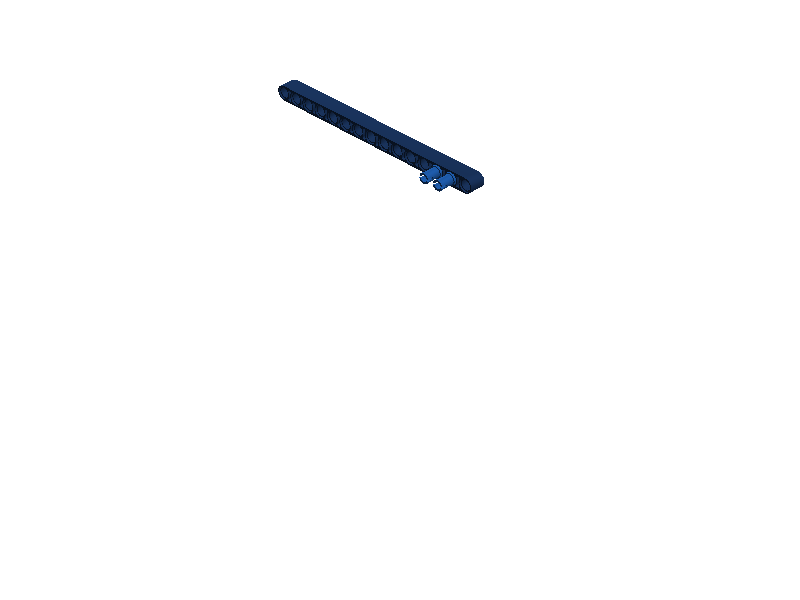
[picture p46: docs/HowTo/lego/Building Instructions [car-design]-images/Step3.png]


Step 4 of 68

- 1 x
- 
- 2 x
- 

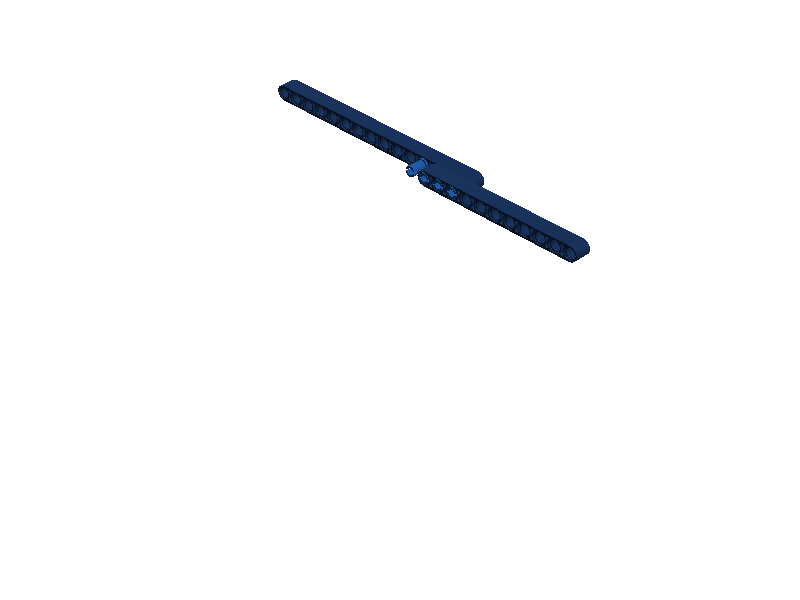
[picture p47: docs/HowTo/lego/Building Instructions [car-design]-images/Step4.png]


Step 5 of 68

- 4 x
- 

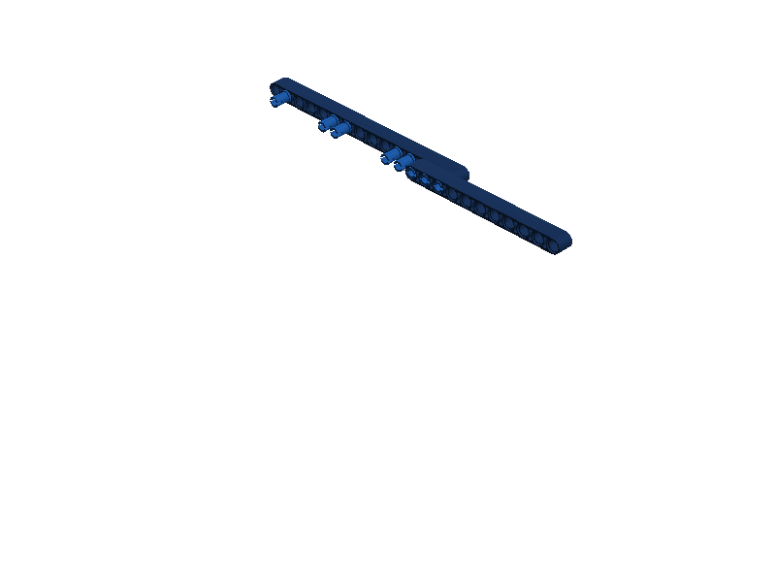
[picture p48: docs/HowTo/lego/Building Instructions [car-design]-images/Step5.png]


Step 6 of 68

- 1 x
- 
- 1 x
- 
- 1 x
- 
- 1 x
- 

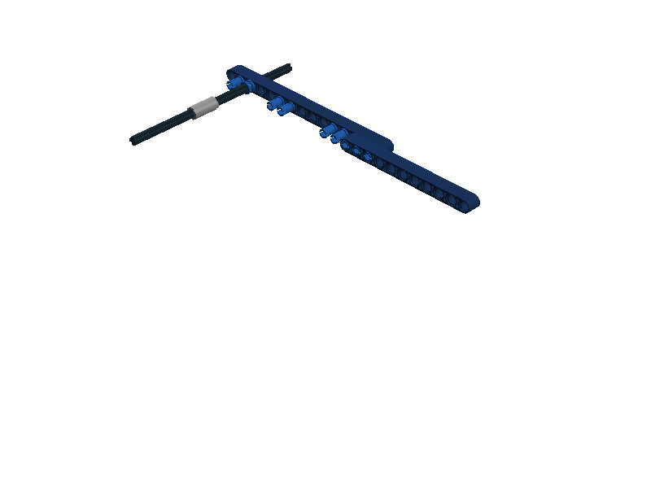
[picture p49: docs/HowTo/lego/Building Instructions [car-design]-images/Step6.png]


Step 7 of 68

- 1 x
- 



Step 8 of 68

- 1 x
- 



Step 9 of 68

- 2 x
- 
- 2 x
- 



Step 10 of 68



Step 11 of 68

- 1 x
- 
- 1 x
- 



Step 12 of 68

- 1 x
- 
- 1 x
- 



Step 13 of 68

- 1 x
- 
- 1 x
- 



Step 14 of 68

- 1 x
- 



Step 15 of 68

- 1 x
- 
- 3 x
- 



Step 16 of 68

- 1 x
- 
- 2 x
- 
- 1 x
- 



Step 17 of 68

- 1 x
- 
- 1 x
- 
- 2 x
- 



Step 18 of 68

- 1 x
- 
- 3 x
- 



Step 19 of 68

- 1 x
- 
- 1 x
- 
- 1 x
- 



Step 20 of 68



Step 21 of 68

- 1 x
- 



Step 22 of 68

- 1 x
- 



Step 23 of 68

- 1 x
- 



Step 24 of 68

- 1 x
- 
- 3 x
- 



Step 25 of 68

- 1 x
- 
- 1 x
- 
- 1 x
- 



Step 26 of 68

- 1 x
- 
- 1 x
- 
- 2 x
- 



Step 27 of 68

- 1 x
- 
- 3 x
- 



Step 28 of 68

- 1 x
- 
- 2 x
- 
- 1 x
- 



Step 29 of 68

- 1 x
- 
- 1 x
- 



Step 30 of 68



Step 31 of 68

- 2 x
- 



Step 32 of 68

- 1 x
- 
- 2 x
- 
- 1 x
- 



Step 33 of 68

- 1 x
- 
- 1 x
- 
- 1 x
- 



Step 34 of 68



Step 35 of 68

- 1 x
- 
- 1 x
- 
- 1 x
- 



Step 36 of 68

- 1 x
- 
- 1 x
- 



Step 37 of 68

- 1 x
- 
- 1 x
- 
- 1 x
- 



Step 38 of 68

- 1 x
- 
- 1 x
- 
- 1 x
- 
- 1 x
- 



Step 39 of 68

- 2 x
- 
- 1 x
- 
- 1 x
- 



Step 40 of 68

- 2 x
- 
- 1 x
- 
- 1 x
- 



Step 41 of 68

- 1 x
- 
- 1 x
- 
- 1 x
- 



Step 42 of 68



Step 43 of 68

- 1 x
- 



Step 44 of 68

- 1 x
- 
- 2 x
- 
- 1 x
- 



Step 45 of 68

- 1 x
- 
- 1 x
- 
- 2 x
- 



Step 46 of 68

- 1 x
- 



Step 47 of 68

- 1 x
- 
- 1 x
- 



Step 48 of 68



Step 49 of 68

- 1 x
- 
- 1 x
- 



Step 50 of 68

- 1 x
- 
- 1 x
- 
- 2 x
- 



Step 51 of 68

- 1 x
- 
- 1 x
- 



Step 52 of 68

- 1 x
- 
- 2 x
- 



Step 53 of 68

- 1 x
- 



Step 54 of 68

- 1 x
- 
- 1 x
- 



Step 55 of 68



Step 56 of 68

- 1 x
- 



Step 57 of 68

- 1 x
- 
- 2 x
- 



Step 58 of 68

- 1 x
- 
- 1 x
- 



Step 59 of 68



Step 60 of 68

- 1 x
- 
- 1 x
- 



Step 61 of 68



Step 62 of 68

- 1 x
- 
- 1 x
- 



Step 63 of 68



Step 64 of 68

- 1 x
- 
- 1 x
- 



Step 65 of 68



Step 66 of 68

- 1 x
- 
- 1 x
- 
- 1 x
- 
- 1 x
- 



Step 67 of 68



Step 68 of 68



4 x |  | 658201 | RIM Ø36.8X20 - White

4 x |  | 658126 | TYRE Ø49.6 X 20 - Black

4 x |  | 4185665 | TECHNIC 2M BEAM - Bright Blue

2 x |  | 4247727 | TECHNIC 3M BEAM - Earth Blue

4 x |  | 4227073 | TECHNIC 5M BEAM - Earth Blue

4 x |  | 4128591 | TECHNIC 5M BEAM - Bright Blue

1 x |  | 3252426 | TECHNIC 7M BEAM - Black

1 x |  | 4154767 | TECHNIC 9M BEAM - Black

4 x |  | 4164358 | TECHNIC 11M BEAM - Earth Blue

3 x |  | 4164422 | TECHNIC 13M BEAM - Black

2 x |  | 4193421 | TECHNIC 13M BEAM - Bright Blue

4 x |  | 6058997 | TECHNIC 15M BEAM - Earth Blue

2 x |  | 6059010 | TECHNIC ANG. BEAM 3X5 90 DEG. - Earth Blue

1 x |  | 4106380 | TECHNIC 5M HALF BEAM - Black

10 x |  | 4260467 | 1/2 BUSH - Bright Blue

1 x |  | 4109810 | 2M CROSS AXLE W. GROOVE - Black

60 x |  | 4129886 | CONNECTOR PEG - Bright Blue

1 x |  | 451926 | CROSS AXLE 3M - Black

2 x |  | 4225927 | CONNECTOR PEG/CROSS AXLE - Bright Blue

1 x |  | 4141814 | BUSH FOR CROSS AXLE - Bright Blue

3 x |  | 4189110 | CONN.BUSH W.FRIC./CROSSALE - Bright Blue

2 x |  | 4514553 | CONNECTOR PEG W. FRICTION 3M - Bright Blue

2 x |  | 4512360 | CROSS AXLE, EXTENSION, 2M - Medium Stone Grey

1 x |  | 4164357 | CATCH W. CROSS HOLE - Earth Blue

1 x |  | 4227273 | CROSS BLOCK 90° - Earth Blue

2 x |  | 370626 | CROSS AXLE 6M - Black

1 x |  | 4185111 | CROSS AXLE 7M - Black

2 x |  | 370726 | CROSS AXLE 8M - Black

2 x |  | 4124045 | CROSS AXLE 5,5 WITH STOP 1M. - Black

2 x |  | 4114670 | TECHNIC STEERING-GEAR 3M - Black

6 x |  | 4195018 | HTO V BEAM 90 DEGR. - Earth Blue

4 x |  | 4158925 | TECHNIC CROSSBLOCK 2X3 - Bright Blue

2 x |  | 4114671 | T. STEERING GEAR, BEARING 2M - Black

1 x |  | 3226901 | DOUBLE CONICAL WHEEL Z20 1M - White

1 x |  | 4211434 | CROWN- AND GEAR WHEEL Z24 - Medium Stone Grey

First | First | | First | First | | Print

© 2012 The LEGO Group. All rights reserved.
Use of the LEGO Digital Designer html print tool, signifies your agreement to the terms of use.

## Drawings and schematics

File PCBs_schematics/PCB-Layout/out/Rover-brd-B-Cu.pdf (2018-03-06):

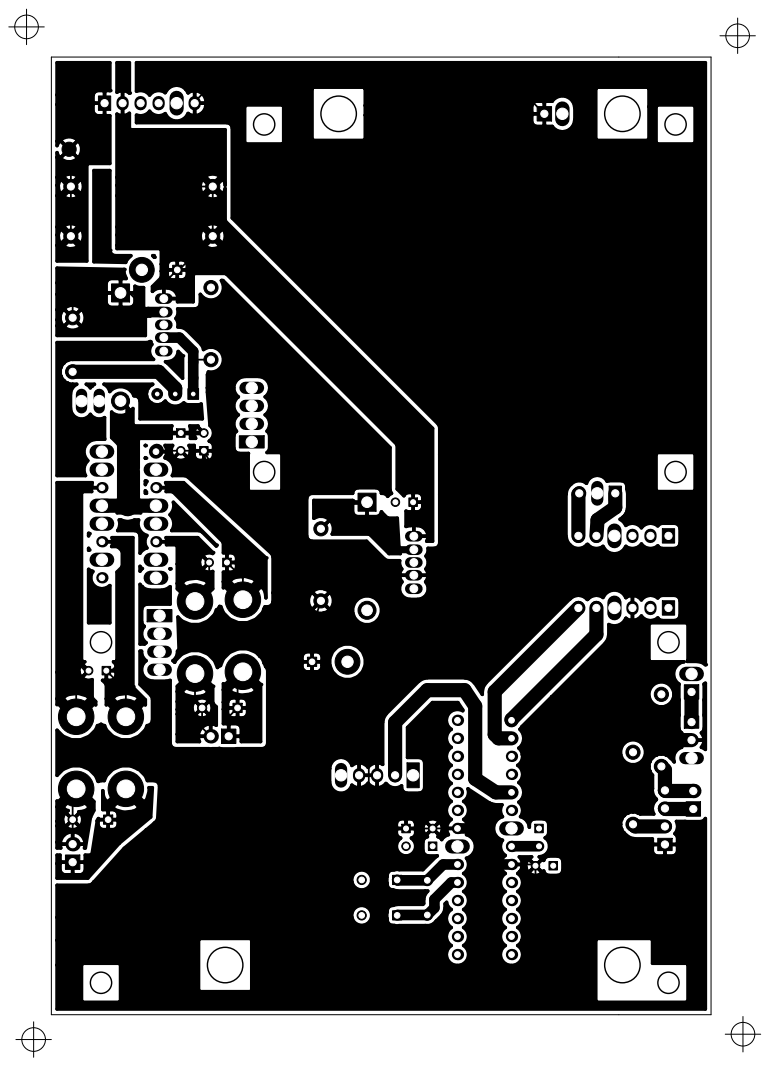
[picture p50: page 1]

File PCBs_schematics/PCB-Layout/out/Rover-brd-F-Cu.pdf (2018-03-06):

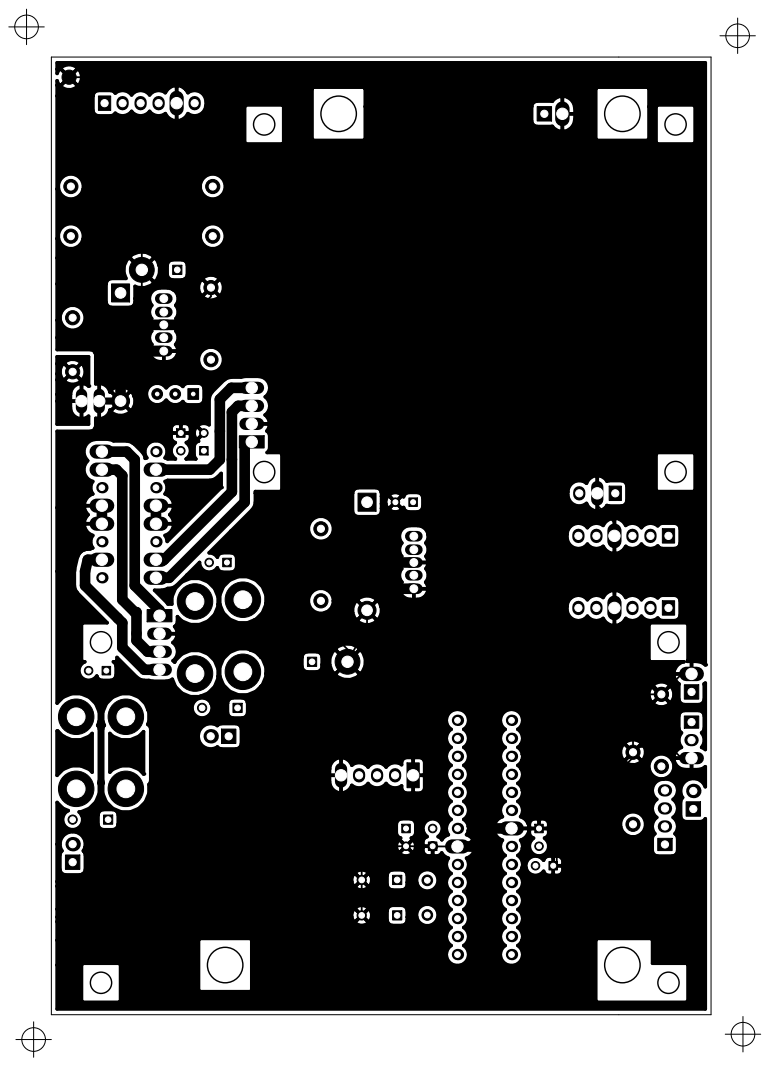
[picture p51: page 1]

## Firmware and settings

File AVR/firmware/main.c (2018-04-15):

/*
 * main.c
 *
 * This program sets the AVR as an analog-digital converter, that can communicate over I2C.
 *
 * MIT License
 *
 * Copyright (c) 2018 Ondřej Masopust; Gymnázium Praha 6, Nad Alejí 1952
 *
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
 * Created on: Dec 29, 2017
 * Author: Ondrej Masopust
 */

#include <avr/io.h>
#include <avr/iomx8.h>
#include <avr/interrupt.h>

/** An array of 2-byte variables that hold the sensor output values.<br>
 * The value under [0] is from the sensor that measures the shorter distances.<br>
 * The value under [1] is from the sensor that measures the larger distances.
 */
uint16_t sensorValues[2];

/**
* A counter, that counts what has been sent over I2C. Base on that, next data is sent.
*/
uint8_t sentCounter = 0;

/**
* The setUpI2C() function is called at the beginning of the program and sets up everything around the I2C.
*/
void setUpI2C(void) {
	// set the device address to be 10 and disable 'general call recognition'
	TWAR = 0b00010100;
	// enable generation of ACK
	TWCR |= (1 << TWEA);
	// enable TWI
	TWCR |= (1 << TWEN);
	// enable TWI interrupt
	TWCR |= (1 << TWIE);
	// clear TWINT flag
	TWCR |= (1 << TWINT);
}

/**
* The i2cStatus() function returns prescaled current state of the I2C.
*
* @return byte containing the status
*/
uint8_t i2cStatus(void) {
	// mask the prescaler bits
	return TWSR & 0b11111000;
}

/**
* The setUpADC() function is called at the beginning of the program and sets up everything around the analog-gigital conversion.
*/
void setUpADC(void) {
	// set the voltage reference to be AVcc
	ADMUX |= (1 << REFS0);
	// enable ADC interrupts
	ADCSRA |= (1 << ADIE);
	// set clock prescaler to be 128
	ADCSRA |= (1 << ADPS2) | (1 << ADPS1) | (1 << ADPS0);
	// disable digital input buffer on all ADC pins except the I2C pins
	DIDR0 |= (1 << ADC3D) | (1 << ADC2D) | (1 << ADC1D) | (1 << ADC0D);
	// enable ADC
	ADCSRA |= (1 << ADEN);
}

/**
* When the adcStartConversion() function is called, a logic 1 is written to the ADSC bit in the ADCSRA register and new analog-digital conversion is started.
*/
void adcStartConversion(void) {
	ADCSRA |= (1 << ADSC);
}

/**
* This interrupt service routine is called when the TWI vector is set. It sends the appropriate data through the I2C and starts new conversion after all.
*/
ISR(TWI_vect) {
	// own SLA+R received, ACK sent || data byte has been transmitted, ACK received
	if (i2cStatus() == 0xA8 || i2cStatus() == 0xB8) {
		switch (sentCounter) {
			case 0:
				// send the MSB of sensorShort
				TWDR = (sensorValues[0] >> 8) & 0xFF;
				break;
			case 1:
				// send the LSB of sensorShort
				TWDR = sensorValues[0] & 0xFF;
				break;
			case 2:
				// send the MSB of sensorLong
				TWDR = (sensorValues[1] >> 8) & 0xFF;
				break;
			case 3:
				// send the LSB of sensorLong
				TWDR = sensorValues[1] & 0xFF;
				// set TWEA to '0' because this is the last byte to be sent
				TWCR &= ~(1 << TWEA);
				break;
		}
		sentCounter++;
		// clear TWINT flag
		TWCR |= (1 << TWINT);

		// data byte has been transmitted and NACK has been received
	} else if (i2cStatus() == 0xC0) {
		// set TWEA to '1' in order to send ACK, when this device is addressed later
		TWCR |= (1 << TWEA);
		sentCounter = 0;
		// clear TWINT flag
		TWCR |= (1 << TWINT);
		// start a new conversion
		adcStartConversion();

		// last data byte has been sent and ACK was received (NACK was expected)
	} else if (i2cStatus() == 0xC8) {
		// just send something random
		TWDR = 0xFF;
		// set TWEA to '1' in order to send ACK, when this device is addressed later
		TWCR |= (1 << TWEA);
		sentCounter = 0;
		// clear TWINT flag
		TWCR |= (1 << TWINT);
		// start a new conversion
		adcStartConversion();
	} else {
		// clear TWINT flag
		TWCR |= (1 << TWINT);
	}
}

/**
* This interrupt service routine is called when the ADC vector is set. It stores the converted value, switches the ADC input to the other sensor and invokes new conversion if needed.
*/
ISR(ADC_vect) {
	// assign a-d conversion result to either [0] or [1] depending on the input selected
	sensorValues[ADMUX & 0x1] = ADCL | ((ADCH << 8) & 0xFF00);
	// switch to the other analog input
	ADMUX ^= 0x1;
	// if this ISR was for the first sensor, start a new conversion for the second sensor
	if (ADMUX & (0x1 == 0x0))
		adcStartConversion();
}

/**
* The main function. It sets everything up, starts first AD conversino and then just hangs in an endless while loop.
*/
int main(void) {
	// set unused pins as inputs
	DDRD &= 0x00;
	DDRC &= 0b11110011;
	DDRB &= 0b11000000;
	// set pull-ups in unused pins - reduce power consumption
	PORTD |= 0xFF;
	PORTC |= 0b00001100;
	PORTB |= 0b00111111;

	setUpI2C();

	setUpADC(); // a first measurement is taken from ADC0
	// start the first conversion
	adcStartConversion();

	// enable interrupts globally
	sei();

	while(1) {

	}

	return 0; // never reached
}

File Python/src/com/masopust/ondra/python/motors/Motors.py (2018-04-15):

#!/usr/bin/env python3.6
'''
Created on Jan 27, 2018

This module contains only the Motor class.

MIT License

Copyright (c) 2018 Ondřej Masopust; Gymnázium Praha 6, Nad Alejí 1952

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

@author: Ondrej Masopust
'''

import RPi.GPIO as gpio


class Motors(object):
    '''
    This class is used to control the motors of the Rover.
    '''

    def __init__(self, pwmOut, directionOut, tcpCommunication):
        '''
        This constructor initializes a new Motor object.
        
        :param pwmOut: The number of the pin that should be used as the output of the PWM
        :type pwmOut: int
        :param directionOut: A list that contains two numbers representing the pins that should be used to control the direction of the rotation.
        :type directionOut: list of ints 
        '''
        gpio.setmode(gpio.BCM)
        self.pwmOut = pwmOut
        self.directionOut = directionOut
        self.tcpCommunication = tcpCommunication
        # set the defined pins to be output
        gpio.setup(self.pwmOut, gpio.OUT)
        gpio.setup(directionOut, gpio.OUT)
        # define a variable that is used to to control the PWM
        # set PWM on the pwmOut pin, 100Hz
        self.pwm = gpio.PWM(self.pwmOut, 100)
        self.pwmRunning = False
        self.currentDutyCycle = 0;
        
    def run(self, dutyCycle):
        '''
        This method starts the PWM. It is pretty similar to the setSpeed() method.
        It either starts the PWM, if stopped, or only changes the duty cycle.
        
        :param dutyCycle: The duty cycle to be applied. 0 <= dutyCycle <= 100
        :type dutyCycle: int
        :raises ValueError: A ValueError is raised when the argument <= 0 or 100 <= argument
        '''
        try:
            if (dutyCycle >= 0 and 100 >= dutyCycle):
                if self.pwmRunning:
                    self.pmw.ChangeDutyCycle(dutyCycle)
                else:
                    self.pwm.start(dutyCycle)
                self.currentDutyCycle = dutyCycle
            else:
                raise ValueError("Motors.run(): Argument out of bounds. Must be: argument <= 0 or 100 <= argument, was: " + dutyCycle)
        except ValueError as err:
            print(err)
            self.tcpCommunication.sendToHost('er' + err)
            
    
    def setSpeed(self, dutyCycle):
        '''
        This method sets the duty cycle of the PWM and thus changes the speed of the motor.
        It is pretty similar to the run() method but if the PWM is stopped,this method does not start it.
        
        :param dutyCycle: The duty cycle to be applied. 0 =< dutyCycle =< 100
        :type dutyCycle: int
        :raises ValueError: A ValueError is raised when the argument <= 0 or 100 <= argument
        '''
        
        try:
            if (dutyCycle >= 0 and 100 >= dutyCycle):
                if self.pwmRunning:
                    self.pmw.ChangeDutyCycle(dutyCycle)
                    self.currentDutyCycle = dutyCycle
            else:
                raise ValueError("Motors.setSpeed(): Argument out of bounds. Must be: argument <= 0 or 100 <= argument, was: " + dutyCycle)
        except ValueError as err:
            print(err)
            self.tcpCommunication.sendToHost('er' + err)

    def speedUp(self, increment):
        '''
        This methods sets a new speed by incrementing the current duty cycle by the given argument if possible.
        
        :param increment: The number that should be added to the current duty cycle
        :type increment: int
        :raises ValueError: A ValueError is raised when the (self.currentDutyCycle + increment) <= 0 or 100 <= (self.currentDutyCycle + increment)
        '''
        try:
            if (self.currentDutyCycle + increment) >= 0 or 100 >= (self.currentDutyCycle + increment):
                if self.pwmRunning:
                    self.pwm.ChangeDutyCycle(self.currentDutyCycle + increment)
            else:
                raise ValueError("Motors.speedUp(): Argument not legal. Must be: (self.currentDutyCycle + increment) >= 0\
                    or 100 >= (self.currentDutyCycle + increment), was: " + self.currentDutyCycle + " + " + increment)
        except ValueError as err:
            print(err)
            self.tcpCommunication.sendToHost('er' + err)

    def setDirection(self, direction):
        '''
        This method sets the rotation direction of the motor.
        
        :param direction: Direction to be applied. An enum *Direction* should be used. 
        :type direction: boolean
        '''
        if direction:
            gpio.output(self.directionOut[0], gpio.HIGH)
            gpio.output(self.directionOut[1], gpio.LOW)
        else:
            gpio.output(self.directionOut[0], gpio.LOW)
            gpio.output(self.directionOut[1], gpio.HIGH)
    
    def getDutyCycle(self):
        '''
        :return: Value of current duty cycle
        :rtype: int
        '''
        return self.currentDutyCycle

    def stop(self):
        '''This method stops the PWM.'''
        self.pwm.stop()
        self.pwmRunning = False
        self.currentDutyCycle = 0;
    
    def clean(self):
        '''This method is called when the client disconnects. It stops the motors and cleans up the GPIO.'''
        self.stop()
        gpio.cleanup()
        

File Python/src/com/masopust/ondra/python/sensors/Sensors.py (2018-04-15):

#!/usr/bin/env python3.6
'''
Created on Sep 4, 2017

This module contains only the Sensors class.

MIT License

Copyright (c) 2018 Ondřej Masopust; Gymnázium Praha 6, Nad Alejí 1952

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

@author: Ondrej Masopust
'''

import threading
import time
import math
import RPi.GPIO as gpio
from smbus2 import SMBusWrapper

from com.masopust.ondra.python.motors.Motors import Motors

class Sensors (threading.Thread):
    '''
    This class is used to control the distance sensor of the Rover.
    '''

    def __init__(self, halt, tcpCommunication):
        '''
        This constructor assigns given arguments to instance variables, sets the thread as daemon and sets up an interrupt
        that is executed when the sensor finishes one rotation.

        :param halt: A threading.Event object, that is used to stop this thread.
            It contains, whether the client disconnected.
        :type halt: threading.Event
        :param tcpCommunication: Instance of the TCPCommunication class that is used to send data to the client.
        :type tcpCommunication: TCPCommunication
        '''
        threading.Thread.__init__(self)
        self.daemon = True
        self.name = "sensorThread"
        
        # This Event contains True when the Raspberry Pi should start to sense another rotation
        self.sensorState = threading.Event()
        
        self.rotationTime = 0
        
        self.halt = halt
        self.tcpCommunication = tcpCommunication
        
        self.sensorMotor = Motors(25, [9, 11], self.tcpCommunication)
        self.sensorMotor.setDirection(True)
        
        # this variable tells if the sensor motor is running
        self.running = False

        gpio.setmode(gpio.BCM)
        # set the pin 22, which is connected to the output of the optolatch, as input
        gpio.setup(22, gpio.IN)
        # set up an interrupt for the optolatch
        gpio.remove_event_detect(22)
        gpio.add_event_detect(22, gpio.FALLING, callback=self.__isr)
        
        self.lastInterruptClock = time.time()

        # time in seconds that it takes for the sensor to take one measurement
        self.CONVERSIONTIME = 0.02
        # this variable counts the initial free rotations when the sensors don't measure yet
        self.rotationCounter = 0
        # this is the variable that tells how many dots will be displayed on the screen
        self.resolution = 0
    
    def run(self):
        '''This method is called when this thread is started by the start() method in the Main class.'''
        self.initSens()
        while not self.halt.is_set() and self.running:
            startTime = time.time()
            message = "dt" + str(self.measure())
            try:
                self.tcpCommunication.sendToHost(message)
            except BrokenPipeError as err:
                break
            endTime = time.time()
            sleepTime = self.CONVERSIONTIME - (endTime - startTime)
            while endTime + sleepTime > time.time():
                pass
        # stop sensor motor
        self.sensorMotor.stop()

        # this only needs to be done, when the sensor is stopped because the client disconnected
        # not only when the sensor was stopped temporarily using the 'stopMeasure' command
        if self.running:
            self.sensorMotor.clean()
            # send ACK back to the main thread
            self.halt.clear()
    
    def initSens(self):
        '''
        This method starts the sensor motor and based on how fast it rotates,
        it counts how many dots will be displayed on the client's computer screen
        and sends this information to the client.
        '''
        if not self.running:
            # reset the rotationCounter
            self.rotationCounter = 0
            self.sensorMotor.run(100)
            self.running = True
            # wait() blocks the flow of the program if Event is not set
            self.sensorState.wait()
            # print("broke")
            # print("initSens() -> self.rotationTime = " + str(self.rotationTime))
            self.resolution = round(self.rotationTime / self.CONVERSIONTIME)
            if not self.halt.is_set():
                self.tcpCommunication.sendToHost("rd")
                self.tcpCommunication.sendToHost("ro" + str(self.resolution))

    def stop(self):
        '''This method stops the direction sensing'''
        self.running = False
        
    def kill(self):
        '''
        This method stops the direction sensing. It is used when the program is
        closed because of a KeyboardInterrupt.
        '''
        self.running = False
        self.sensorMotor.stop()
        self.sensorMotor.clean()
    
    def measure(self):
        '''
        This method reads the data from the AVR and returns the measured distance
        
        :return: Measured distance
        :rtype: int
        '''
        with SMBusWrapper(1) as bus:
            val = bus.read_i2c_block_data(0x0A, 0, 4)
            longSensor = int((val[2] << 8) | val[3])
            longVoltage = longSensor * (5 / 1024)
            if longVoltage == 0:
                # so that we don't get the math domain error
                longVoltage = 1
            longDist = round(916.64 * math.pow(longVoltage, -2.236))
        return longDist
        
    def getRunning(self):
        '''
        :return: The state of sensing
        :rtype: boolean
        '''
        return self.running
    
    def __isr(self, channel):
        '''
        This interrupt service routine is called automatically when the optolatch changes its state.
        This function counts the time that it takes for the sensor to make one turn. This function is private.
        
        :param channel: Number of the pin that caused the interrupt
        :type channel: int
        '''
        # The signal edges form the optolatch are noisy so it produces more than one
        # interrupt when there should be only one. That is why there is this
        # condition - to clean the undesired interrupts
        self.rotationTime = time.time() - self.lastInterruptClock
        if self.rotationTime > 1.3:
            # print("\nnow")
            # print("self.rotationTime = " + str(self.rotationTime))
            self.lastInterruptClock = time.time()
            if self.rotationCounter == 2:
                # tell, that the sensor thread should start sensing
                self.sensorState.set()
            # this is needed when initializing the sensor. The sensor motor makes some free
            # rotations to examine how fast it rotates.
            if self.rotationCounter < 3:
                self.rotationCounter += 1
            else:
                # send the RESETDOTCOUNTER command
                self.tcpCommunication.sendToHost("rc")
            

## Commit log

2017-08-16 fixed bug where I couldn't access Pane from Java code
    [Main.java]
2017-08-17 threads are working properly
2017-08-17 connection thread extends Task<Void>
2017-08-20 error messages are written to the preloader
    [Main.java]
2017-09-01 added server socket testing class that doesn't work properly
2017-10-21 styled the whole app and changed arrow key events to switch-case
2017-11-13 deleted compiled files and edited .gitignore to not track these files
2017-12-31 I2C test were successful
    [Rover.kicad_pcb, Rover.sch]
2018-01-03 AVR code is working for 2 sensors
2018-01-20 percentage added to the application and motor and servo drivers tested on RPi
    [Rover.sch]
2018-01-27 edited schematics, progress on the Rover software
    [Rover.sch]
2018-02-01 md edit
    [Rover.sch]
2018-02-02 commented all necessary in the Python code and renamed PCBs folder to PCBs_schematics
    [Rover.kicad_pcb, Rover.sch]
2018-02-03 deleted I2C class from the python code as it ws not used
2018-02-03 Java app can display errors in red, Python sometimes sends them and some more work done
    [Main.java, Motors.py, Sensors.py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]
2018-02-05 Java app receives 'dt' correctly
    [Sensors.py]
2018-02-23 added 6V buck-converter version to the schematic
    [Rover-general.sch]
2018-03-03 progress on the PCB
    [Rover.kicad_pcb, Rover.sch]
2018-03-06 more progress on the PCBs
    [Rover-B.Cu.gbr, Rover-B.Mask.gbr, Rover-B.SilkS.gbr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]
2018-03-07 ferrite beads pads smallered
    [Rover.kicad_pcb]
2018-03-07 edited pcb files for production
    [Rover-B.Cu.gbr, Rover-B.Mask.gbr, Rover-B.SilkS.gbr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]
2018-03-15 first step of designing mounts of the PCB on the Rover
    [Rover.kicad_pcb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]
2018-03-16 final Rover design
    [car-BOM.xlsx]
2018-03-23 added building instructions for the Rover
    [Rover.kicad_pcb]
2018-03-30 fixed defining unused pins on the AVR for lower power consumption
    [main.c]
2018-03-30 renamed General-scheme folder
    [Rover.kicad_pcb, Rover.sch]
2018-03-30 added the ability to stop the sensor temporarily
2018-03-31 renamed folder and added value to the crytal
    [Rover.kicad_pcb, Rover.sch]
2018-04-02 servo works, main motor changes direction, but the enums for changing directions are not treated as booleans
2018-04-02 edited Rover lego design
    [car-BOM.xlsx]
2018-04-02 deleted I2C.rtf from the git repo
2018-04-04 fixed AVR I2C bug, now it responses to the i2cdetect
    [main.c]
2018-04-11 exchanged threading.Event instead of queue, between main thread and sensor thread
2018-04-13 sensing still does not work as expected
    [InterruptTest.py, Sensors.py, speedTest.py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]
2018-04-13 Python code shortened, processing data is fast enough
    [Sensors.py]
2018-04-13 Java code accepts new type of 'dt' messages, but hangs on quit when the sensor is running
2018-04-14 servo is centered
2018-04-14 edited Lego design - removed differential
    [car-BOM.xlsx]
2018-04-14 Python program does not print neither rotation time nor the number of sent data
2018-04-15 edited car-BOM.xlsx
    [car-BOM.xlsx]
2018-04-15 solved some FIXMEs and deleted the rest of them
    [Motors.py]
